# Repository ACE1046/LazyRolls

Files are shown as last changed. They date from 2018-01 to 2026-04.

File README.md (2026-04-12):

# LazyRolls

Automatic motorized roller blinds project.

Моторизированный привод для рулонных штор. Управление по Wi-Fi. Питание внешнее. Возможна интеграция в системы умного дома.




### Ссылки
Описание проекта: [https://mysku.club/blog/diy/62110.html](https://mysku.club/blog/diy/62110.html)\
Файлы для печати: [https://www.thingiverse.com/thing:2857899](https://www.thingiverse.com/thing:2857899)\
Видео работы: [https://www.youtube.com/watch?v=lvBh_m7pOAI](https://www.youtube.com/watch?v=lvBh_m7pOAI)

### Плагины для систем умного дома
[Domoticz](https://github.com/ACE1046/LazyRollsDomoticz)\
[Hubitat Elevation](https://github.com/yix/Hubitat/blob/master/drivers/LazyRolls.groovy) (Автор [yix](https://github.com/yix))\
Home Assistant (встроенная поддержка через MQTT Discovery с версии 0.09)\
[Homebridge](https://github.com/vitva/Lazyroll-settings-for-homebridge) (Автор Vitva)\
[Управление с пульта ИК / RF433](https://mysku.club/blog/diy/87912.html) (Автор SamoS)\
[Карточка управления шторами для HA](https://github.com/samoswall/pic-shutter-card) (Автор SamoS)\
[Android приложение для управления шторами](https://github.com/samoswall/LazyRoll-Android-App) (Автор SamoS)

### Структура директорий

Firmware - готовые прошивки\
Source - исходный код\
Source\data - файлы для SPIFFS. Иконка, css-стили, java scripts\
Board - файлы схемы и платы для DipTrace\
Board\Gerbers - gerber files для заказа плат на фабрике\
3D_parts - OpenSCAD и stl для печати

### Changelog

05.04.2018 v0.01 beta
* Более-менее рабочая версия с настройками. Не всё доделано, многого не хватает.

07.04.2018 v0.02 beta
* Автосоздание файлов CSS и favicon в SPIFFS при их отсутствии/обновлении.

28.04.2018 v0.03 beta
* Исправлен баг с закрытием шторы после перезагрузки.
* Добавлена работа по расписанию.

22.02.2019 v0.05 beta
* Управление двигателями идёт в прерывании, увеличилась плавность работы двигателя и отзывчивость интерфейса.
* Номера пинов 4 и 5 исправлены, теперь типичное подключение ABCD. Настройки менять не надо.
* Концевик можно инвертировать (нормальнозамкнутый - нормальноразомкнутый). Актуально для датчика Холла вместо концевика.
* Добавлен http-запрос /set?pos=X (X = 0 - 100, в процентах).
* Состояние можно получить в виде XML по адресу /xml.
* Прошивка откомпилирована с поддержкой модулей с флеш памятью PUYA.
* Отображается размер SPIFFS, ссылка на форматирование появляется при ошибке файловой системы.

16.03.2019 v0.06
* Добавлен протокол MQTT. Описание настроек http://imlazy.ru/rolls/mqtt.html

10.04.2019 v0.07
* Добавлена встроенная в esp8266 подтяжка пина концевика. На платах NodeMCU и тому подобных, отпадает необходимость во внешнем резисторе, R8 по схеме.
* Добавлена настройка безопасного порога, количество шагов, при которых штора игнорирует концевик, пока не выползет из зоны его действия. Для герконов и датчиков Холла можно установить значение больше стандартных 100.

02.06.2020 v0.08
* Сделан плавный пуск двигателя. Это чуть повысило мощность мотора и максимальную скорость, но незначительно. Пока в черновой реализации и без какой-либо настройки.
* Прошивка проверена и скомпилирована с Arduino core for ESP8266 v2.7.1. Исправило отваливание wi-fi сети в некоторых случаях.
* Исправлен баг в JavaScript, из-за которого иногда лагал веб интерфейс, при загрузке страниц и сразу после.
* Во время движения по MQTT в формате JSON сообщается не только текущее положение, но и точка назначения (destination, в процентах).
* Синий светодиод теперь используется. Он кратко моргает при подаче питания. После каждой неудачной попытки подключиться к основной
сети зажигается на 1 секунду. Если к сети подключиться с трёх попыток не вышло, светодиод горит непрерывно, значит создана собственная WiFi сеть.
(Оранжевый светодиод программно не управляется, подключен напрямую к питанию. Его можно только отпаять/откусить/заклеить.)
В нормальной работе функцию диода можно указать в настройках, а также менять по http/mqtt. Более подробно [imlazy.ru/rolls/led.html](http://imlazy.ru/rolls/led.html).
* Отображается напряжение питания для новых плат. На старых, при желании, можно допаять два резистора. Цепочка Vin - 150K - esp_adc - 10K - GND.
* Исправлен баг с максимальным количеством шагов игнорирования концевика при опускании шторы. Теперь работают значения более 255. До 65000. Актуально для герконов и датчиков Холла. Спасибо acu73.
* Исправлен баг с невозможностью указать порт MQTT сервера более 9999. Спасибо George Tkachenko.

29.01.2021 v0.09
* Исправлен баг со сбивающимся временем.
* Пресеты для точного позиционирования шторы. Актуально для штор день/ночь. Положения задаются в настройках. Могут использоваться в расписании.
* Добавлены команды для MQTT. "=NNNNN" (без кавычек) - позиционирование шторы в шагах. "@N" - переход к пресету N.
* Добавлен http-запрос /set?steps=NNNNN (NNNNN = 0 - 65000, в шагах мотора).
* Добавлен http-запрос /set?preset=N (N = 1 - 5). Переход в заданное положение.
* Добавлено автоматическое перенаправление на страницу настроек при подключении к шторе в режиме точки доступа (первоначальная настройка).
* Добавлены MQTT-комманды open и close. Равнозначны on и off. Для удобства интеграции с HA.
* Добавлен MQTT Discovery для Home Assistant. Включается в настройках, автоматически добавляет штору в HA.
* Библиотека для работы с MQTT изменена с AdaFruit на PubSubClient (by Nicholas O'Leary).
* Концевик может быть установлен на полностью закрытое положение, вместо открытого. Например, для жалюзи.
* Проценты в MQTT командах и статусах можно поменять на обратные, т.е. 0% значит закрыто, 100% - открыто. Так по умолчанию считает Cover в Home Assistant.

30.03.2021 v0.10
* Исправлен баг с количеством шагов игнорирования концевика. Фактическое было в 8 раз меньше указанного в настройках.
* Повышена точность измерения напряжения, на платах с резисторами на ADC.
* Добавлена поддержка драйверов Step/Dir моторов (например, NEMA17). Можно подключать двигатели и драйвера от 3D принтеров. Распиновка пока фиксированная, En 4, Step 13, Dir 12.
* Минимальное время шага уменьшено до 50 мкс (было 100). Этого должно хватить, чтобы крутить обычный NEMA17 на практически максимальной скорости при 1/16 шага.
* В MQTT добавлен топик присутствия (alive/живой). В него отправляется "online" при подключении к MQTT и "offline" при отключении, в т.ч. аварийном, по "завещанию" (LWT). В Home Assistant используется как availability topic, для определения состояния привода.
* В настройках можно изменить количество шагов, которое привод прокручивает вверх в поисках концевика после предполагаемого нуля. Если поставить 0, запаса не будет. Если поставить большое число, будет дольше крутить вверх, пока не сработает концевик. Но в случае проблем с концевиком, может привести к перегреву мотора или поломке шторы. Менять не рекомендуется.
* Добавлена возможность подключения кнопки для управления. Подключается на Gnd и один из пинов GPIO 0(DTR)/2/3(RX), который выбирается в настройках. При движении нажатие кнопки останавливает штору, двойное нажатие - останавливает и перезапускает в противоположном направлении. Долгое нажатие (1 секунда) - отправляет в первый пресет или во второй, если штора уже в первом.
* Синий диод можно настроить на мигание при нажатии на кнопку.
* Легкий редизайн внешнего вида, в первую очередь мобильной версии. JS-код вынесен в отдельный файл в spiffs.
* Статичные файлы сжаты gzip'ом.
* Обновлена страница /update, добавлены подсказки по перепрошивке.

05.08.2021 v0.11
* Экспериментальная фича: режим мастер/ведомый по проводу. Подробнее [imlazy.ru/rolls/master.html](http://imlazy.ru/rolls/master.html).
* Помимо кнопки, можно задействовать ещё один дополнительный вход. Например, для геркона, определяющего открытие окна. Статус передаётся по MQTT в выбранный топик.
* Новый топик MQTT, сообщает в формате JSON состояние (ip, rssi, uptime, voltage, aux_input). При включенном HA MQTT Discovery, автоматически добавляет эти сенсоры в Home Assistant.
* (v0.11.2) Исправлен баг с получением времени по NTP при старте.

09.11.2021 v0.11.3
* Исправлен баг с отображением hostname в сети. В XML статус добавлен hostname. Разрешена отдача XML сторонним страницам (CORS). Спасибо Samos.

27.01.2022 v0.12
* В MQTT Discovery добавлены фичи Home Assistant 2021.11: ссылка на страницу конфигурации (visit device), доп. статусы попадают в раздел "Diagnostic".
* Добавлены команды click, longclick для MQTT и /set?click, /set?longclick для HTTP. Делают то же самое, что и кнопка управления (открыть/закрыть/стоп; пресет1/2). Для работы этих команд, включать аппаратную кнопку не требуется.
* Можно изменить название шторы в настройках, для удобства. Отображается в заголовке окна и в поле name в XML.
* Настройка статического IP.
* При прошивке на чистый модуль поле SSID остаётся пустым и привод сразу стартует в режиме точки доступа, а не пытается приконнектиться к несуществующей сети lazyrolls.
* Исправлена (надеюсь) верстка страницы расписания.
* Проект модифицирован для компиляции в PlatformIO, но можно откомпилировать и в ArduinoIDE. Часть кода переписана для экономии памяти. Arduino core for ESP8266 обновлено до v3.0.2.
* Добавлен лог событий. Открывается в веб-интерфейсе по ссылке из блока информации. Лог на английском, но думаю там и так понятно. Отображаются основные события, причина перезагрузки, отвалы от сети и mqtt-сервера, срабатывание концевика в движении, синхронизация времени. Для отладки возможных проблем.

10.12.2022 v0.13
* Поддержка приемника 433МГц.
* Восход и закат в расписании.
* Поддержка двух физических кнопок с возможностью выбирать действие по нажатию и, в режиме мастера, кем управлять. Можно сделать раздельные кнопки Открыть и Закрыть, а можно разделить кнопки для управления только этой шторой и всей группой.
* На главную страницу добавлены кнопки пресетов. В режиме мастера добавлен выбор, кем управлять, всеми, этой шторой или ведомыми.
* В режиме мастера можно в расписании раздельно управлять ведущим и ведомыми.
* Можно задать пароль для режима точки доступа, создаваемой после включения привода при отсутствии Wi-Fi.

26.01.2023 v0.13.1
* Добавлена единица измерения для напряжения в Home Assistant.

20.04.2023 v0.14
* Добавлена поддержка моторов постоянного тока, в том числе с энкодером. Подробнее [imlazy.ru/rolls/motor.html](http://imlazy.ru/rolls/motor.html).
* Добавлен второй концевик, на противоположной стороне.
* Добавлены команды MQTT. По команде "report" сообщает по MQTT свой статус. Командой "endstop" можно эмулировать нажатие концевика, например, zigbee датчиком открытия двери.
* По MQTT отправляются статусы open / opening / close / closing / stopped для Home Assistant.
* Добавлен gratuitous ARP. Привод постоянно сообщает свой IP в сети. Включается автоматически, если не используется MQTT. Может предотвратить некоторые случаи недоступности привода в сети.
* Сенсор Uptime в Home Assistant заменен на сенсор Last Restart Time. В mqtt топик info отправляются и аптайм, как раньше, и время рестарта.

16.01.2024 v0.15
* Плавный старт шагового мотора стал более плавным.
* Arduino core for ESP8266 обновлено до v3.1.2.
* Откомпилированные прошивки теперь универсальны, подходят для любого размера флэш-памяти.
* Изменения в MQTT: Обновлена интеграция с Home Assistant для совместимости с последней версией. Для наименования устройства используется не сетевое имя (hostname), а название (name), если оно заполнено в настройках. Недопустимые символы заменяются на подчеркивание, hostname теперь может содержать точку, без ошибки в логах HA.
* Retained команды удаляются и игнорируются при подключении к MQTT.
* В xml статус добавлены вход aux (если настроен), поле 'master' (значение 'yes' для мастера, 'no' - все остальные) и список пресетов и их значений.
* В настройках можно выбрать две скорости мотора. Их можно использовать, к примеру, для ручного (быстро) и автоматического (тихо) управления или для разных скоростей вверх и вниз. Вторую скорость можно использовать при управлении по расписанию, http, mqtt, rf и кнопками.
* Все настройки можно скачать/загрузить в виде файла на странице обновления прошивки.
* Команды для сброса положения и поиска нуля заново: 'zero' по mqtt, /set?zero по http. Команда 'reboot' по mqtt для перезагрузки.
* Сторожевой пингер. Включается в настройках. Раз в минуту пингует заданный IP (например, wifi-роутер). После неудачи, пинги повторяются каждые 10 секунд. 4 пропущенных подряд пинга записываются в Log. После 7 пропущенных пингов выполняется указанное в настройках действие (логирование / переподключение / перезагрузка). Интервал пинга и количество пропущенных пингов можно изменить константами PINGER_INTERVAL_S / PINGER_REPEAT_INTERVAL_S / PINGER_WARN / PINGER_ACTION в прошивке, при необходимости.
* Режим мастер/ведомый по WiFi. Теперь в дополнение к ведомым по проводу можно добавить ведомых по IP. На них распространяются все возможности управления, как и у проводных. Поддерживается до 10 ведомых в 5 группах (те же, что у проводных. В одной группе могут быть как проводные, так и беспроводные ведомые). Подробнее [imlazy.ru/rolls/master.html](http://imlazy.ru/rolls/master.html).
* В настройках добавлены кнопки включения WiFi у проводных ведомых, с отображением их IP после подключения к сети, для удобства настройки ведомых.
* В расписании можно установить самое раннее время срабатывания по солнцу, например "на рассвете, но не ранее 07:00".
* Положение шторы можно сохранять во flash-памяти, оно не теряется при перезагрузке. Включается в настройках. Не рекомендуется использовать без необходимости, ресурс памяти на запись ограничен, это может сократить срок службы. Если перезагрузка произойдет во время движения, положение не восстановится и потребуется поиск нуля.

17.01.2024 v0.15.2
* Исправлен баг, не появлялись кнопка Scan и пункт добавления IP в настройках wifi ведомых.
* Исправлен баг в wifi мастер/слейв режиме.

18.01.2024 v0.15.3
* Исправлен баг работы wifi мастер/слейв от аппаратных кнопок.
* При смене направления движения штора останавливает и плавно начинает двигаться в обратную сторону.
* Включена поддержка mDNS.

06.03.2025 v0.15.4
* Поддержка ESP32. Пока что тестовый вариант для ESP32-C3. Должно работать с ABCD мотором (другие пока не проверялись). Компиляция в Platformio IDE (в Arduino IDE не проверялось).

10.04.2026 v0.15.6
* Для шаговых двигателей добавлена плавная остановка при движении вниз. В настройках можно включить удержание мотора в течение ~5 сек после остановки, для предотвращения разматывания шторы по инерции.
* Для DC моторов можно регулировать скорость через PWM не только на драйверах с отдельным входом PWM, но и через пины управления вращением, если драйвер поддерживает.
* На esp32c3 отображается температура чипа.
* Добавлена поддержка выбора часового пояса в формате POSIX с учётом перевода на летнее время. Добавлен справочник часовых поясов по городам.
* Диапазон уровней солнца над горизонтом в расписании увеличен до [-10, 10] градусов.
* Добавлена функция принудительного поиска нуля для кнопок и RF пульта. К командам для сброса нуля ('zero' по mqtt, /set?zero по http) добавлены 'gotozero' и /set?gotozero для поиска нуля прямо сейчас.

### Authors

* **ACE** - [e-mail](mailto:ace@imlazy.ru)

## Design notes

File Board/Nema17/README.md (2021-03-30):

# LazyRolls with NEMA17

Поддержка Step/Dir драйверов шаговых двигателей добавлена с версии v0.10 прошивки.\
Step/Dir drivers support added to v0.10 firmware.

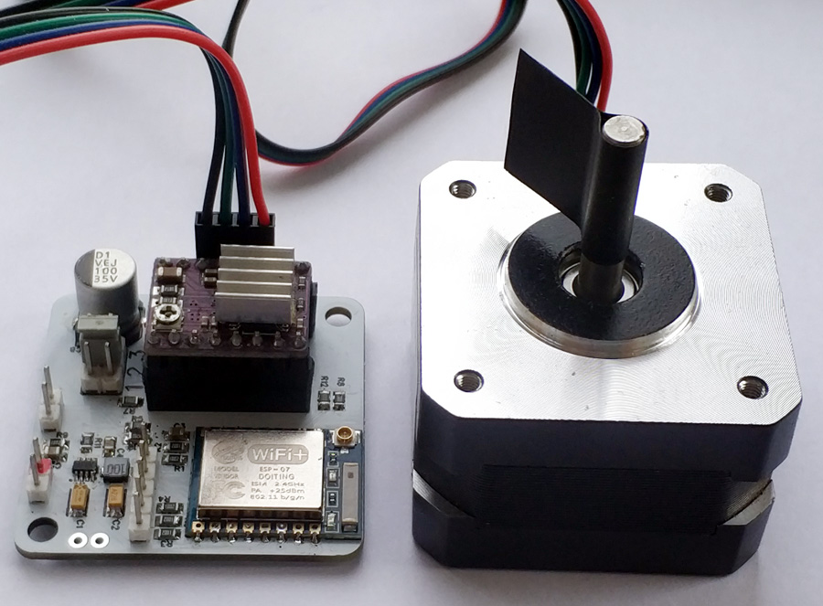
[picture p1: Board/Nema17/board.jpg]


### Подключение / Wiring

Enable - GPIO4\
Step - GPIO13\
Dir - GPIO12

### Плата / Board

Размер платы равен размеру мотора NEMA17, 42х42мм\
Board size equal to NEMA17 motor size, 42x42mm

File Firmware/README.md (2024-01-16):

### Прошивки для привода LazyRolls

Начиная с версии 0.15 прошивка стала универсальной (_auto), на любой размер памяти. И переименована по имени проекта, LazyRoll.\
Обновлять прошивку по воздуху, через интерфейс штор, можно (и нужно) прямо архивом .gz, не распаковывая.\
Файлы *.1MByte.bin для плат с модулем ESP07.\
Файлы *.4MByte.bin для собранных на основе Wemos, NodeMCU и т.д.\
Размер памяти можно уточнить в веб-интерфейсе привода.

Обновление прошивки на ту же версию или более новую сохраняет все настройки. Обновление на предыдущую - стирает настройки, включая WiFi.

### LazyRolls firmware

Starting from version 0.15, the firmware became universal (_auto), for any memory size. And renamed after the project name, LazyRoll.\
When updating the firmware over the air, through web interface, upload .gz archive, without unpacking it.\
Choose *.1MByte.bin for boards with ESP07 module\
Choose *.4MByte.bin for devices based on Wemos, NodeMCU, etc\
Memory size can be seen in web-interface.

Updating to newer version will preserve settings, but downgrading to previous will erase all settings, including WiFi.

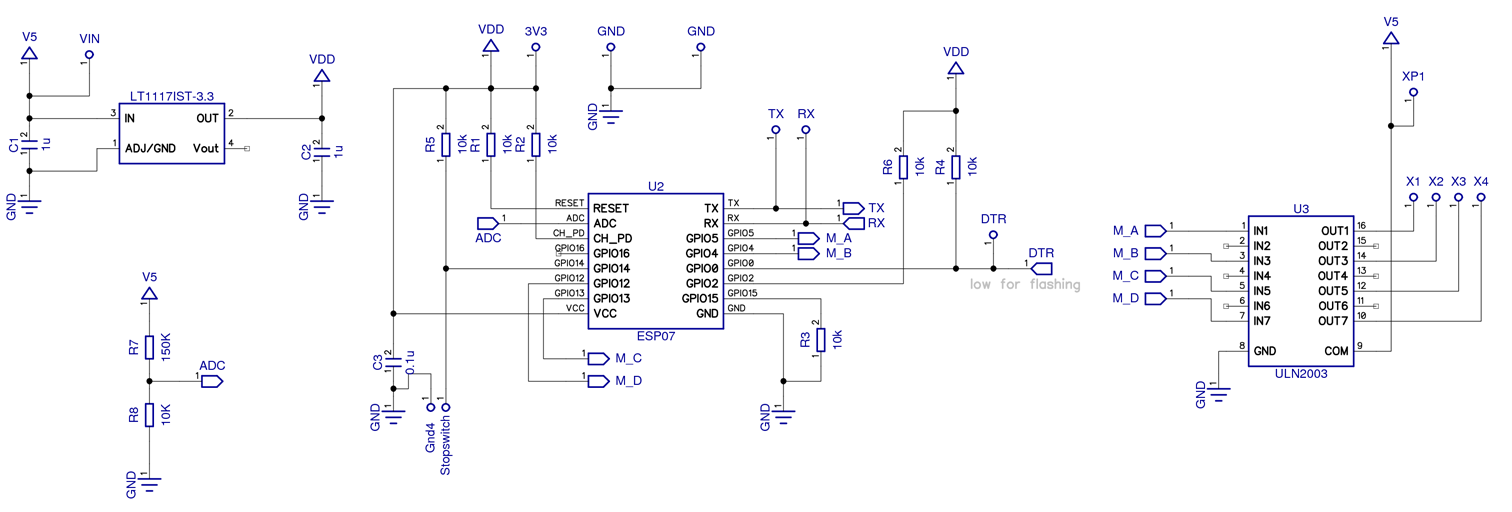
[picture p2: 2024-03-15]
Board/scheme.png

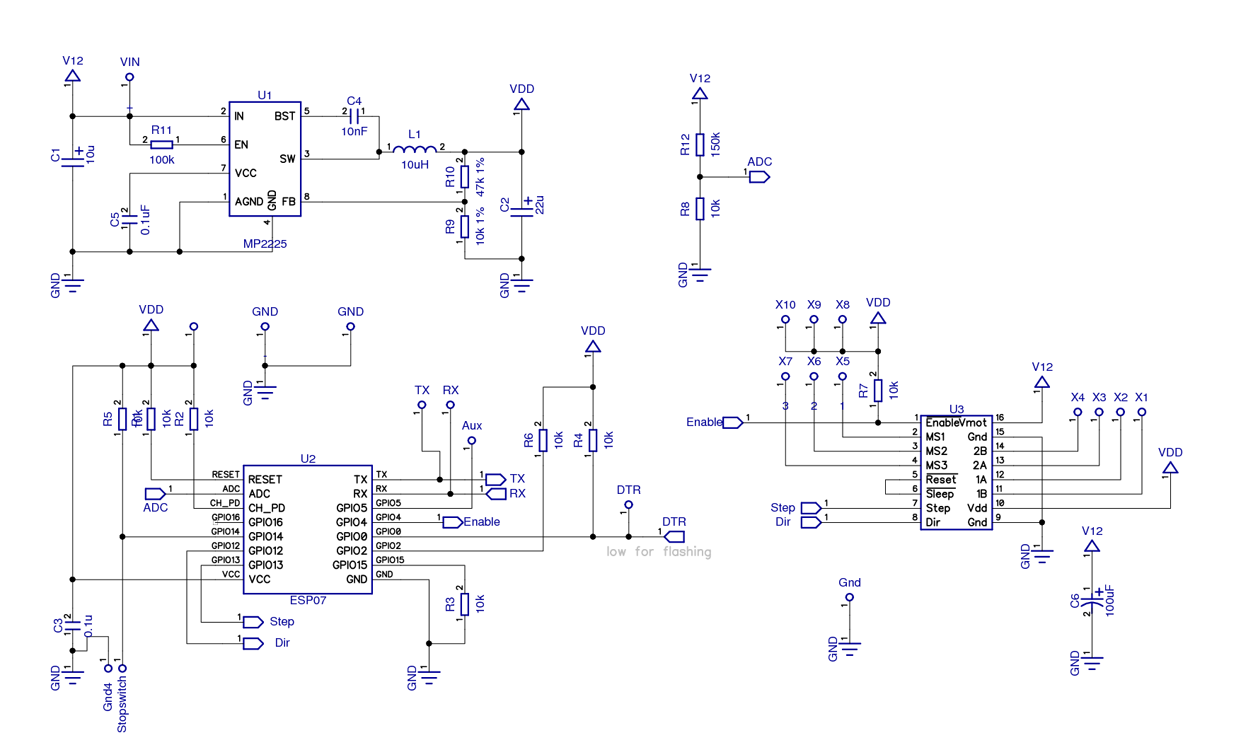
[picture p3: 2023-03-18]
Board/Nema17/LazyRolls_v1.2_nema17.png

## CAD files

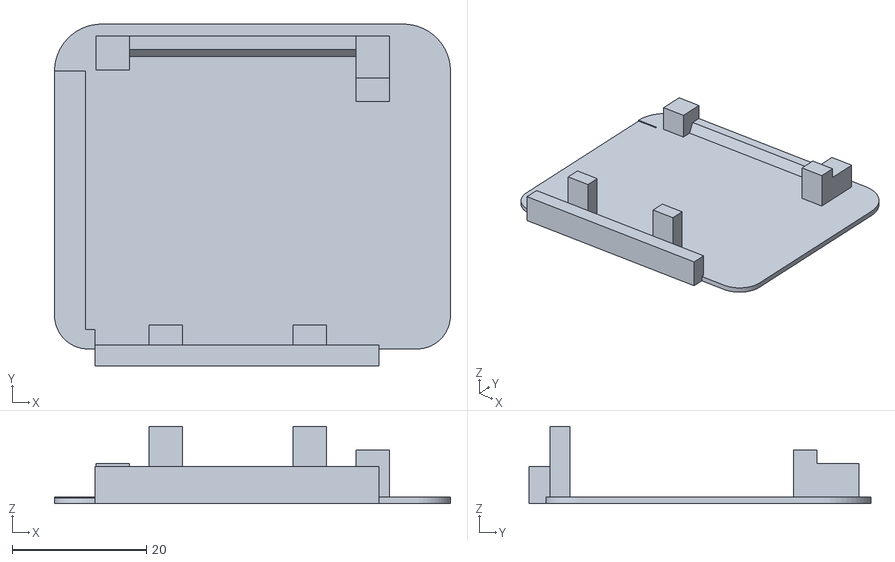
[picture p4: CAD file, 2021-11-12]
3D_parts/cap.stl
59.0 x 50.9 x 11.5

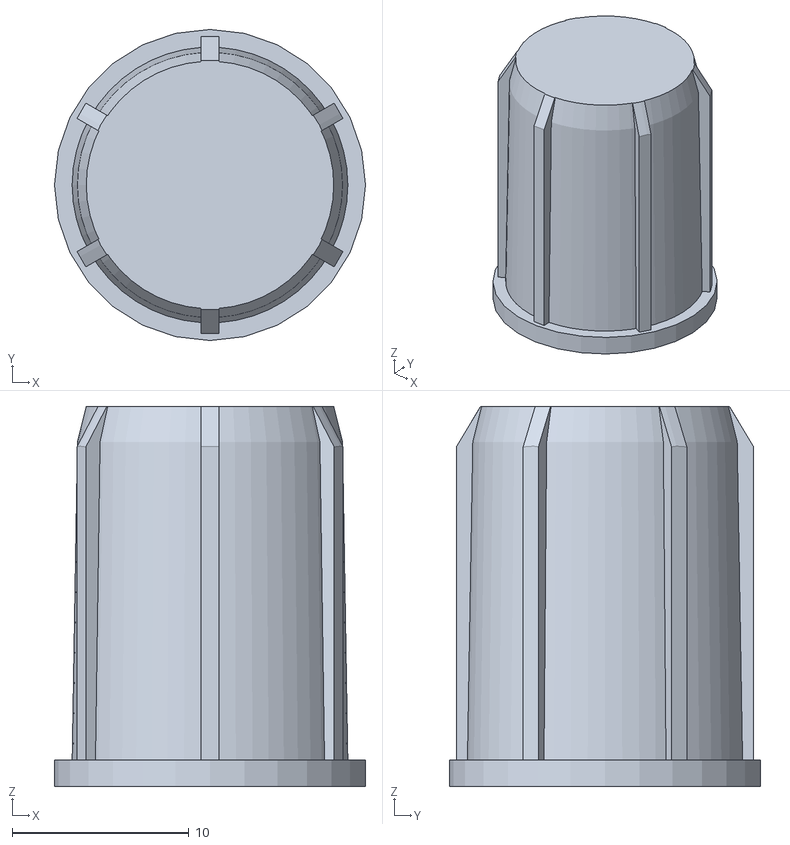
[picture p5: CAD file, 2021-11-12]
3D_parts/Shaft.stl
17.6 x 17.6 x 21.5

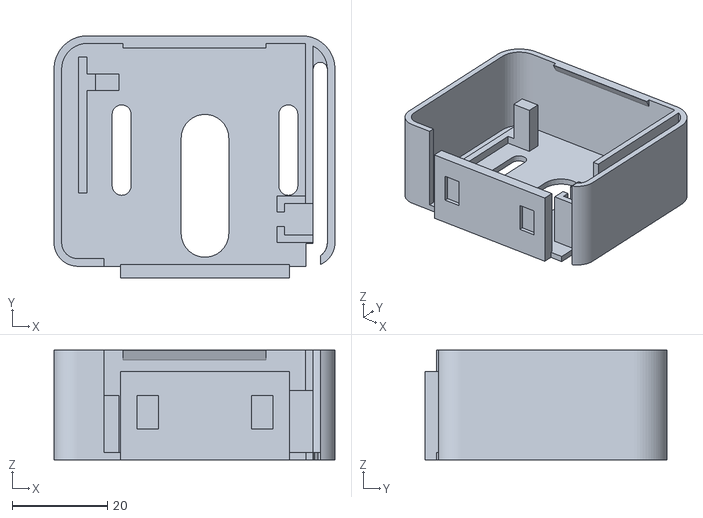
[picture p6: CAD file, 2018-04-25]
3D_parts/Motor_bracket.stl
59.0 x 50.9 x 23.0

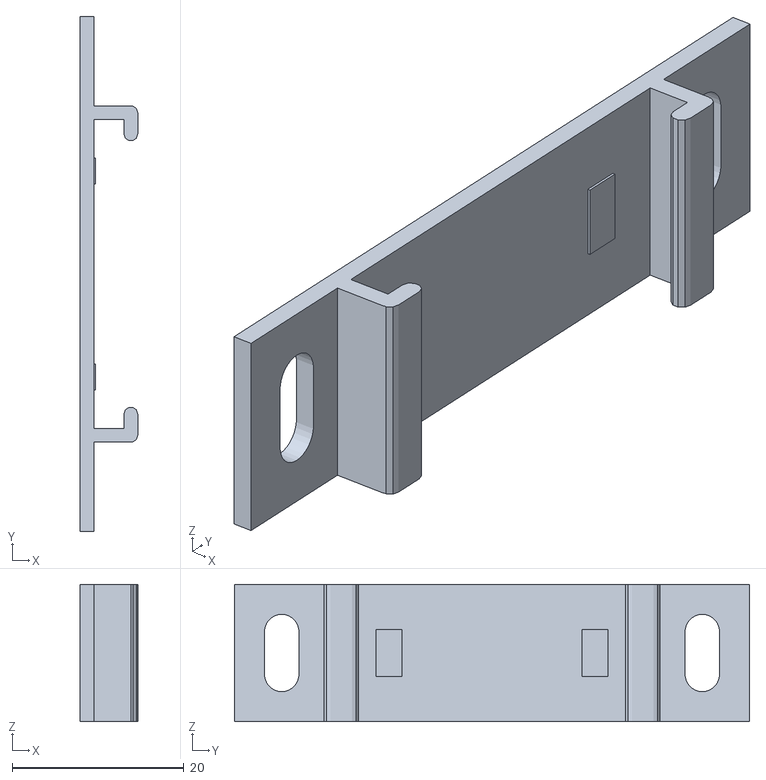
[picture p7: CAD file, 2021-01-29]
3D_parts/mount_screw.stl
6.70 x 60.0 x 16.0

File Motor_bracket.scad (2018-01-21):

base_h=35.5;
base_w=17;
base_t=3.0;
base_space=base_h+7; //42;

fix_h=4.5;
fix_w=7;
fix_d=24/2;

arm_t=1.5;
arm_l=46.5;
arm_w=10;
arm_dist=35/2;
arm_hole=4;
arm_hole_l1=15;
arm_hole_l2=30;

side_t=1.6;
full_h=59;
full_w=21.5;
back_r=5;
front_r=7;
sw_hole=3;
sw_t=1.6;
b_o=1;

motor_hole_w=10;
motor_hole_l=30;
motor_shift=2.2;

//micro switch
msw_w=6+0.6;
msw_h=7;
msw_l=13;
msw_t=1.6;
msw_conn=3;

// cap
cap_t=1.0;
cap_sp=0.4; // space
cap_fix_h=5;
cap_fix_t=2;
cap_fix_w=5;
cap_fix_ofs=4.5;
lock_h=2;
lock_w=30;

module arm()
{
	hull()
	{
		translate([0, arm_hole_l1, -arm_t-1]) cylinder(h=arm_t+2, d=arm_hole, $fn=20);
		translate([0, arm_hole_l2, -arm_t-1]) cylinder(h=arm_t+2, d=arm_hole, $fn=20);
	}
}

module sides(hh, r_b, r_f, b, shrink)
{
	hull()
	{
	translate([ full_h/2-r_b, r_b-side_ofs, -b]) cylinder(h=hh+arm_t, r=r_b-shrink);
	translate([-full_h/2+r_b, r_b-side_ofs, -b]) cylinder(h=hh+arm_t, r=r_b-shrink);
	translate([ full_h/2-r_f, arm_l-r_f, -b]) cylinder(h=hh+arm_t, r=r_f-shrink);
	translate([-full_h/2+r_f, arm_l-r_f, -b]) cylinder(h=hh+arm_t, r=r_f-shrink);
	}
}

side_ofs=base_t-b_o;

module base()
{
	translate([motor_shift,0,0]) difference()
	{
		translate([-base_h/2, -base_t, -arm_t]) cube([base_h, base_t, base_w+arm_t]);
		translate([-fix_d-fix_h/2, -base_t-1, arm_w/2]) cube([fix_h, 2, fix_w]);
		translate([ fix_d-fix_h/2, -base_t-1, arm_w/2]) cube([fix_h, 2, fix_w]);
	}

	difference()
	{
		sides(full_w, back_r, front_r, arm_t, 0, $fn=70);
		sides(full_w+2, back_r, front_r, 0, side_t, $fn=40);
		translate([-base_space/2+motor_shift, -side_t-1, 0]) cube([base_space+sw_hole, side_t+2, full_w+1]);
		mirror([1,0,0])
		translate([-arm_dist-motor_shift, 0, 0]) arm();
		translate([-arm_dist+motor_shift, 0, 0]) arm();
		//translate([-motor_hole_w/2+motor_shift, 0, -base_t-1]) cube([motor_hole_w, arm_l-side_t, base_t+2]);
		hull()
		{
			translate([motor_shift, motor_hole_w/2, -base_t-1]) cylinder(d=motor_hole_w, h=base_t+2, $fn=30);
			translate([motor_shift, -motor_hole_w/2+motor_hole_l, -base_t-1]) cylinder(d=motor_hole_w, h=base_t+2, $fn=30);
		}
		
		
		translate([full_h/2-sw_t-sw_hole, back_r-side_ofs, -arm_t-1]) cube([sw_hole, arm_l+side_ofs-back_r-front_r, arm_t+full_w+2]);
		translate([full_h/2-sw_t-sw_hole/2, arm_l-front_r, -arm_t-1]) cylinder(h=arm_t+full_w+2, r=sw_hole/2, $fn=10);
		intersection()
		{
			translate([ full_h/2-back_r, back_r-side_ofs, -arm_t-1]) cylinder(h=full_w+arm_t+2, r=back_r-sw_t, $fn=30);
			translate([ full_h/2-sw_t-sw_hole, back_r-side_ofs-10+0.01, -arm_t-1]) cube([10,10,full_w+arm_t+2]);
		}
		translate([+base_space/2+motor_shift, -side_t-1, -arm_t-1]) cube([sw_hole, side_t+2, full_w+1]);

	}

	translate([full_h/2-sw_t-sw_hole-msw_h-msw_t+msw_h+msw_t-side_t, back_r-side_ofs+msw_w+msw_t*2-side_t, 0]) 
	cube([side_t, arm_l-(back_r-side_ofs)-(msw_w+msw_t*2), full_w]);
	// microswitch
	translate([full_h/2-sw_t-sw_hole-msw_h-msw_t, back_r-side_ofs, 0]) 
	difference()
	{
		cube([msw_h+msw_t, msw_w+msw_t*2, msw_l]);
		translate([msw_t, msw_t, 0]) cube([msw_h+1, msw_w, msw_l+1]);
		translate([-1, msw_t+msw_w/2-msw_conn/2, 0]) cube([msw_t+2, msw_conn, msw_l+1]);
	}

	// PCB holder
	translate([-full_h/2+side_t+2+1.5+1.5+2.5, 35, 0]) cube([5, 3.5, 12]);
	translate([-full_h/2+side_t+2+1.5, 35, 0]) cube([5+1.5+2.5, 3.5, 2]);
	translate([-full_h/2+side_t+2+1.5, 12, 0]) cube([1.8, 30, 2]);

	%translate([-full_h/2+side_t+2, 0, 0])
	{
		color("green") cube([1.5, 43.2, 21]);
		color("blue") translate([1.5,21.9,3])cube([1.5, 21, 16]);
		color("grey") translate([3,23.5,5])cube([2.5, 15, 12]);
	}

	// lock
	hull()
	{
		translate([-lock_w/2, arm_l-side_t-lock_h/2, full_w-0.1]) cube([lock_w, side_t, 0.1]);
		translate([-lock_w/2, arm_l-side_t, full_w-lock_h]) cube([lock_w, side_t, 0.1]);
	}
}

module cap()
{
  difference()
	{
		hull()
		{
			$fn=50;
			translate([ full_h/2-back_r, back_r-side_ofs, 0]) cylinder(h=cap_t, r=back_r);
			translate([-full_h/2+back_r, back_r-side_ofs, 0]) cylinder(h=cap_t, r=back_r);
			translate([ full_h/2-front_r, arm_l-front_r, 0]) cylinder(h=cap_t, r=front_r);
			translate([-full_h/2+front_r, arm_l-front_r, 0]) cylinder(h=cap_t, r=front_r);
		}
		translate([full_h/2-sw_t-sw_hole, back_r-side_ofs-100, -cap_t+cap_sp]) cube([sw_hole+100, arm_l+side_ofs-back_r-front_r+100, cap_t]);
		translate([+base_space/2+motor_shift, -side_t-1, -cap_t+cap_sp]) cube([sw_hole, side_t+2, cap_t]);
	}
	translate([motor_shift-base_space/2+cap_sp, -base_t, -full_w+base_w]) cube([base_space-cap_sp, base_t+cap_sp, full_w-base_w+cap_t]);
	translate([motor_shift-base_h/2+cap_fix_ofs, cap_sp, -(full_w-base_w+cap_t+cap_fix_h)]) cube([cap_fix_w, 3, full_w-base_w+cap_t+cap_fix_h]);
	translate([motor_shift+base_h/2-cap_fix_ofs-cap_fix_w, cap_sp, -(full_w-base_w+cap_t+cap_fix_h)]) cube([cap_fix_w, 3, full_w-base_w+cap_t+cap_fix_h]);
	translate([-full_h/2+side_t+2+1.5+1.5+2.5, 35, -cap_fix_h-2]) cube([5, 3.5, cap_fix_h+2]);
	translate([-full_h/2+side_t+2+1.5+1.5+2.5, 35, -cap_fix_h]) cube([5, arm_l-35-side_t-cap_sp, cap_fix_h]);

	// front lock
	hull()
	{
		translate([-full_h/2+side_t+2+1.5+1.5+2.5, arm_l-side_t-2-cap_sp-lock_h/2,  0]) cube([full_h-front_r-side_t-(2+1.5+1.5+2.5), 2, 0.1]);
		translate([-full_h/2+side_t+2+1.5+1.5+2.5, arm_l-side_t-2-cap_sp, -lock_h]) cube([full_h-front_r-side_t-(2+1.5+1.5+2.5), 2, 0.1]);
	}

	translate([full_h/2-sw_t-sw_hole-side_t-5, 35-5+arm_l-35-side_t-cap_sp, -cap_fix_h]) cube([5, 5, cap_fix_h]);
	// mswitch
//	translate([full_h/2-sw_t-sw_hole-msw_h-msw_t, back_r-side_ofs, -(full_w-msw_l)]) 
//		cube([msw_h+msw_t, msw_w+msw_t*2, full_w-msw_l]);
}

//base(); //translate([0, 0, full_w+0.2]) cap();
rotate([0,180,0]) cap();

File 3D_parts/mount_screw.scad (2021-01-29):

// base plate
bw=16;
bl=60;
bt=1.6;

// mount
mw=16;
ml=36;
mh=3.5;
mt=1.6;
ma=2.5; // arms

//pads
pw=5.5;
pl=3;
ph=0.2;
po=12;

// holes
hd=4;
hl=5;
ho=24.5;

module hole(offset, diam)
{
  hull()
  {
    translate([-hl/2, offset, -1]) cylinder(h=bt*2+2, d=diam, center=true, $fn=30);
    translate([ hl/2, offset, -1]) cylinder(h=bt*2+2, d=diam, center=true, $fn=30);
  }
}

//rotate([0,90,0])
{
    difference()
    {
      union()
      {
        translate([-bw/2, -bl/2, -bt]) cube([bw, bl, bt]);

        translate([0, po,0]) cube([pw, pl, ph*2], center=true);
        translate([0,-po,0]) cube([pw, pl, ph*2], center=true);
      }
      hole(-ho, hd);
      hole(ho, hd);
    }

    translate([-bw/2, -ml/2-mt, -bt]) cube([mw, mt, bt+mh+mt/2]);
    translate([-bw/2,  ml/2, -bt]) cube([mw, mt, bt+mh+mt/2]);

    hull()
    {
        translate([0, -ml/2+ma-mt/2, mh+mt/2]) rotate([0, 90, 0]) cylinder(h=mw, d=mt, center=true, $fn=10);
        translate([0, -ml/2-mt/2, mh+mt/2]) rotate([0, 90, 0]) cylinder(h=mw, d=mt, center=true, $fn=10);
    }

    hull()
    {
        translate([0, ml/2-ma+mt/2, mh+mt/2]) rotate([0, 90, 0]) cylinder(h=mw, d=mt, center=true, $fn=10);
        translate([0, ml/2+mt/2, mh+mt/2]) rotate([0, 90, 0]) cylinder(h=mw, d=mt, center=true, $fn=10);
    }
}

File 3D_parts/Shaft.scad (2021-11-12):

d=15.6;
l=20;
cone=2;

// base
bd=d+2;
bl=1.5;

// shaft
sd=5.3;
sw=3.2;
sl=7;

difference()
{
	intersection()
	{
		union()
		{
			translate([0, 0, -bl]) cylinder(h=bl, d=bd);
			translate([0, 0, 0]) cylinder(h=l-cone, d1=d, d2=d-0.6, $fn=50);
			translate([0, 0, l-cone]) cylinder(h=cone, d1=d-0.6, d2=d-0.6-cone/2, $fn=50);

			
			rotate([0, 0,  0]) translate([0, 0, l/2]) cube([1, d+1.2, l], center=true);
			rotate([0, 0, 60]) translate([0, 0, l/2]) cube([1, d+1.2, l], center=true);
			rotate([0, 0,-60]) translate([0, 0, l/2]) cube([1, d+1.2, l], center=true);
		}
		translate([0, 0, -bl-0.1]) cylinder(h=l+bl+0.2, d1=l*2, d2=d-0.6-cone/2, $fn=50);
	}
	intersection()
	{
		translate([0, 0, -bl-0.1]) cylinder(h=sl, d=sd, $fn=40);
		translate([0, 0, sl/2-bl-0.1]) cube([sw, sd, sl], center=true);
	}
}

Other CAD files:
3D_parts/Motor_bracket.scad

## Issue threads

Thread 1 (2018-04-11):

Ссылка на муську в README

Bougakov, 2018-04-11:
Пожалуйста, поставьте ссылку на свою статью https://mysku.ru/blog/diy/62110.html в README.md, а то ж не найти потом... Спасибо!

ACE1046, 2018-04-11:
Благодарю! Совсем забыл про это.
Сделано.

T-REX-XP, 2019-08-19:
Во время тестирования, замечаю странное поведение. Шторы не работатю вместе на одном окне. То ли теряют подключение к wifi, толи в сон входят. Пробовал разносить по разным блоками питания и по разным сетям wifi. Первое время после старта вроде доступны обе админки и можно управлять, но когда на ночь оставляешь что утром только одна открывается.

Closed 2018-04-11.

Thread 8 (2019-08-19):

Шторы не работают одновременно

T-REX-XP, 2019-08-19:
Во время тестирования, замечаю странное поведение. Шторы не работатю вместе на одном окне. То ли теряют подключение к wifi, толи в сон входят. Пробовал разносить по разным блоками питания и по разным сетям wifi. Первое время после старта вроде доступны обе админки и можно управлять, но когда на ночь оставляешь что утром только одна открывается.

Closed 2019-09-24.

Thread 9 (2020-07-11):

Добавить ссылку на Hubitat driver

yix, 2020-07-11:
Я запили LazyRolls драйвер для IoT хаба Hubitat Elevation. Хочу поделиться его кодом, возмоно кому-то окажется полезным.

https://github.com/yix/Hubitat/blob/master/drivers/LazyRolls.groovy

Closed 2020-07-13.

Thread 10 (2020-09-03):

Кнопки для управления.

VadimSVI, 2020-09-03:
Отличная работ! Считаю, что кроме удаленного управления, не хватает физических кнопок для управления шторами. Не всегда удобно заходить на веб интерфейс, а наличие отдельных кнопок позволит при необходимости быстро управлять ими.

ACE1046, 2021-03-30:
Возможность подключить физическую кнопку добавлена в версии v0.10

Closed 2021-03-30.

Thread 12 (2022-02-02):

Неявная работа после сброса питания (save/restore position in eeprom?)

andrew-moiseyev, 2022-02-02:
Антон, спасибо за проект!

Есть один неочевидный и нигде не отражённый момент - после подачи питания кнопки теста работают корректно, нажатие "вниз" делает "вверх". Если кому-то тоже будет непонятно - в setup:
```
// start position is twice as fully open. So on first close we will go up till home position
position=ini.full_length*2+ini.up_safe_limit;
```

Предложения:
1. Сделать это очевидным - отразить в документации, выдавать предупреждение в web-части, отдавать в mqtt.
2. Всё же сохранять в eeprom - говорят про 100.000 записей и неограниченное чтение. Если писать 10 раз в день - это 27 лет. Делаем метод SetPosition, в нём присваивание position и запись в eeprom. В сетапе, соответственно, считывание и присваивание напрямую. Для подстраховки от отключения питания во время работы мотора - сохранять признак isRolling, если после возобновления питания он true - работать по Вашему алгоритму.

ACE1046, 2022-02-02:
Спасибо за фидбек!

Да, этот момент у многих пользователей вызывает вопросы при первоначальной настройке. Где-то с 0.10й версии прошивки я добавил на главном экране, с большими кнопками, комментарий внизу:
> Напоминание. После перезагрузки, по любой команде (открыть или закрыть) штора вначале едет вверх, до концевика, чтобы найти нулевую точку. Это нормально.

Вопросов стало меньше (в почте, личке, тг-канале). Над документацией, конечно, ещё работать и работать. При первом старте, пожалуй, больше ничего не сделать.

При обычной работе это не должно быть заметно вообще, если шторы используются в режиме полного открывания/закрывания. И если питание не отключалось настолько, что был пропущен очередной момент переключения. Открытая штора (у концевика) закрывается сразу, закрытая - так и так едет в сторону концевика. Проблема только если из [полу]закрытого состояния получаем команду на закрытие или определенный процент. Имхо, не такой уж частый сценарий.

Сохранять положение я уже думал. Наверное, сделаю, хотя бы для пробы. Вообще, у esp8266 нет eeprom. Можно использовать часть внешней флеш-памяти программ. Китайцы в модули паяют разные чипы, разных производителей, разного качества. Сколько там циклов, я не знаю. Хорошо, если стандартные для микроконтроллеров 10000. При минимуме 4 записи в сутки (два цикла, запись перед и после) - 7 лет. Терпимо, если так. Конечно, можно будет провести ускоренное испытание, для гарантии. И использовать распределение записи на несколько ячеек.

Ещё момент, почему я изначально не хотел так делать, неизвестно, что вообще происходило в то время, что не было питания. Может штору механически закрыли. А привод помнит открытое состояние и пытается её размотать ещё больше. Может и ничего страшного, конечно. Но точно потребует ручной настройки, чтобы пришло в норму.

Думаю, вариант, как сейчас, всё-таки оптимальный. Но опцию сохранения положения запишу в to do, постараюсь сделать, для тех, кому оно нужно.

andrew-moiseyev, 2022-02-02:
Собрали NodeMCU + драйвер + мотор, без концевика. Начали крутить - тесты крутят в обе стороны, вниз - крутит вверх. Напоминания не читали, разумеется. Может, в сетапе ставить флаг "wasMoved=false" и пока ни разу не крутили - показывать предупреждение _над_ кнопками красным/заметным цветом? С чекбоксом "да понял я, не показывайте больше".

andrew-moiseyev, 2022-02-02:
И на сайт бы ссылку на гитхаб.

ACE1046, 2022-02-02:
Принято, продумаю этот момент. Этот Issue пусть повисит открытым, чтобы не забыть.

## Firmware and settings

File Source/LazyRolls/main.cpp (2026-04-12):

/*
LazyRolls
(C) 2019-2022 ACE, a_c_e@mail.ru
http://imlazy.ru/rolls/

21.12.2018 v0.04 beta
21.02.2019 v0.05 beta
16.03.2019 v0.06
10.04.2019 v0.07
02.06.2020 v0.08
29.01.2021 v0.09
30.03.2021 v0.10
05.08.2021 v0.11
27.01.2022 v0.12
09.12.2022 v0.13
20.04.2023 v0.14
16.01.2024 v0.15

*/
#ifdef ESP8266
	#include <ESP8266WiFi.h>
	#include <ESP8266WebServer.h>
	#include <ESP8266HTTPUpdateServer.h>
	#include <ESP8266HTTPClient.h>
	#include <ping.h>
	#include <FS.h>
#else
	#include <WiFi.h>
	#include <WebServer.h>
	#include <HTTPUpdateServer.h>
	#include <HTTPClient.h>
	#include "ping32.h"
	#include "FS.h"
	#include <LittleFS.h>
//	#include <rom/rtc.h> // for reset reason
	#if CONFIG_IDF_TARGET_ESP32C3
	#include "esp32c3/rom/spi_flash.h"
	#endif
	//#include "driver/gpio.h"
	//gpio_get_level(gpio_num_t gpio_num);
	#include "hal/gpio_hal.h"
	#include "driver/temperature_sensor.h"
	#define SPIFFS LittleFS
	#define GPOS GPIO.out_w1ts.val
	#define GPOC GPIO.out_w1tc.val
	#define GPI GPIO.in.val
	#include <esp_task_wdt.h>
	#define ESP32_WDT_TIMEOUT 10000  // WDT timeout
#endif
#include <WiFiUdp.h>
#include <DNSServer.h>
#include <time.h>
#include "settings.h"
extern "C" {
#include "lwip/etharp.h" // gratuitous arp
#include "lwip/tcpip.h" // gratuitous arp
}

#define VERSION "0.15.6"
#define MQTT 1 // MQTT & HA functionality
#define ARDUINO_OTA 1 // Firmware update from Arduino IDE
#define MDNSC 1 // mDNS responder. Required for ArduinoIDE web port discovery
#define DAYLIGHT 1 // Sunrise functions
#define RF 1 // RF receiver support
#define SPIFFS_AUTO_INIT
#define SWAP_AB_CD 0

#if FLASH_MAP_SUPPORT
#define AUTOMEMSIZE
#include <flash_hal.h>
// Custom memory map, 128K SPIFFS for 1MB modules, 1M for 4MB
#define FLASH_MAP_LAZYROLL \
	{ \
		{ .eeprom_start = 0x402fb000, .fs_start = 0x402db000, .fs_end = 0x402fb000, .fs_block_size = 0x1000, .fs_page_size = 0x100, .flash_size_kb = 1024 }, \
		{ .eeprom_start = 0x403fb000, .fs_start = 0x403c0000, .fs_end = 0x403fb000, .fs_block_size = 0x1000, .fs_page_size = 0x100, .flash_size_kb = 2048 }, \
		{ .eeprom_start = 0x405fb000, .fs_start = 0x40500000, .fs_end = 0x405fa000, .fs_block_size = 0x2000, .fs_page_size = 0x100, .flash_size_kb = 4096 }, \
		{ .eeprom_start = 0x409fb000, .fs_start = 0x40400000, .fs_end = 0x409fa000, .fs_block_size = 0x2000, .fs_page_size = 0x100, .flash_size_kb = 8192 }, \
		{ .eeprom_start = 0x411fb000, .fs_start = 0x40400000, .fs_end = 0x411fa000, .fs_block_size = 0x2000, .fs_page_size = 0x100, .flash_size_kb = 16384 }, \
		{ .eeprom_start = 0x4027b000, .fs_start = 0x40273000, .fs_end = 0x4027b000, .fs_block_size = 0x1000, .fs_page_size = 0x100, .flash_size_kb = 512 }, \
	}
  FLASH_MAP_SETUP_CONFIG(FLASH_MAP_LAZYROLL);
#endif

#include "spiff_files.h"

#if MDNSC
	#ifdef ESP8266
		#include <ESP8266mDNS.h>
	#else
		#include <ESPmDNS.h>
	#endif
#endif

#if MQTT
	// For MQTT support: Sketch - Include Library - Manage Libraries - PubSubClient - Install
	#include <PubSubClient.h>
#endif

#if ARDUINO_OTA
	#include <ArduinoOTA.h>
#endif

#if RF
	// For RF support: Sketch - Include Library - Manage Libraries - rc-switch by Suat Ozgur - Install
	#include "RCSwitch.h"
	RCSwitch mySwitch = RCSwitch();
#endif

#if DAYLIGHT
	#include "daylight.h"
#endif

// copy "wifi_settings.example.h" to "wifi_settings.h" and modify it, if you wish
// Or comment next string and change defaults in this file
//#include "wifi_settings.h"

#ifndef SSID_AND_PASS
// if "wifi_settings.h" not included
const char def_ssid[] PROGMEM = ""; // Empty ssid to create SoftAP at start
const char def_password[] PROGMEM = "";
const char def_ntpserver[] PROGMEM = "ru.pool.ntp.org";
const char def_hostname[] PROGMEM = "lazyroll-%06X";
const char def_mqtt_server[] PROGMEM = "mqtt.lan";
const char def_mqtt_login[] PROGMEM = "";
const char def_mqtt_password[] PROGMEM = "";
const uint16_t def_mqtt_port=1883;
const char def_mqtt_topic_state[] PROGMEM = "lazyroll/%HOSTNAME%/state";
const char def_mqtt_topic_command[] PROGMEM = "lazyroll/%HOSTNAME%/command";
const char def_mqtt_topic_alive[] PROGMEM = "lazyroll/%HOSTNAME%/alive";
const char def_mqtt_topic_aux[] PROGMEM = "lazyroll/%HOSTNAME%/aux";
const char def_mqtt_topic_info[] PROGMEM = "lazyroll/%HOSTNAME%/info";
#endif

//char *temp_host;
const char* update_path = "/update2";
const char* update_username = "admin";
const char* update_password = "admin";
uint16_t def_step_delay_mks = 1500;
#define FAV_FILE "/favicon.ico"
#define CLASS_FILE "/styles.css"
#define JS_FILE "/scripts.js"
#define INI_FILE "/settings.ini"
#define POS_FILE "/position.dat"
#ifdef ESP8266
#define PIN_SWITCH 14
#if SWAP_AB_CD
#define PIN_A 13
#define PIN_B 12
#define PIN_C 5
#define PIN_D 4
#else
#define PIN_A 5
#define PIN_B 4
#define PIN_C 13
#define PIN_D 12
#endif
#define PIN_EN 4
#define PIN_ST 13
#define PIN_DR 12
#define PIN_LED 2
uint8_t PIN_PWM = 15;
#else
#define PIN_SWITCH 7
#define PIN_A 4
#define PIN_B 3
#define PIN_C 6
#define PIN_D 5
#define PIN_EN 3
#define PIN_ST 6
#define PIN_DR 5
#define PIN_LED 8
//#define PIN_PWM 4 // ?
uint8_t PIN_PWM = 4;
#define PIN_ADC 0 // voltage
#endif
#define PIN_ENC_A PIN_C
#define PIN_ENC_B PIN_D
#define DIR_UP (-1)
#define DIR_DN (1)
#define MAX_PINOUT 8 // Motor types. 3xStepper + 1 step/dir + 4 DC/PWM/Enc
#define DEFAULT_UP_SAFE_LIMIT 300 // make extra rotations up if not hit switch
#define DEFAULT_SWITCH_IGNORE_STEPS 100 // ignore endstop for first step on moving down
#define MIN_STEP_DELAY 50 // minimal motor step time in mks
#define UART_PING_INTERVAL_MS (30*1000) // Master ping slaves every 30 seconds
#define SLAVE_MAX_NO_PING_MS (70*1000) // Enable WiFi in slave mode if no ping from master
#define SLAVE_SLEEP_TIMEOUT_MS (180*1000) // Disable WiFi in slave mode after network idle
#define PINGER_WARN 4 // Log sfter N ping fails
#define PINGER_ACTION 7 // Action (log/reconnect/reboot) after N ping fails
#define PINGER_INTERVAL_S 60 // Ping interval, seconds
#define PINGER_REPEAT_INTERVAL_S 10 // Ping interval after ping fail, seconds
#define ALARMS 10
#define DAY (24*60*60) // day length in seconds
#define STRINGIFY(x) #x
#define TOSTRING(x) STRINGIFY(x)
#define ARRAYSIZE(arr) (sizeof(arr) / sizeof(arr[0]))
#define MASTER (ini.slave == 255)
#define SLAVE (ini.slave != 255 && ini.slave != 0)
#define ADDR_MASTER 0
#define ADDR_SELF_ONLY 0
#define ADDR_ALL 255
#define ADDR_DEFAULT 254
#define MQTT_INFO_SECONDS 1*60 // Send mqtt info (rssi, uptime, etc) every N seconds
#define MOTOR_OFF_DELAY 10000 // Delay before powering off stepper motor (around 1 sec)
#define STEPS_BREAKING 25 // Decrease speed on last steps

const int Languages = 2;
const char ru_ru[] PROGMEM = "Русский";
const char en_en[] PROGMEM = "English";
const __FlashStringHelper *Language[Languages]={ (__FlashStringHelper*)en_en, (__FlashStringHelper*)ru_ru };
const PROGMEM char *onoff[][Languages]={{"off", "on"}, {"выкл", "вкл"}};

const uint8_t steps[3][4]={
	{PIN_A, PIN_C, PIN_B, PIN_D},
	{PIN_A, PIN_B, PIN_D, PIN_C},
	{PIN_A, PIN_B, PIN_C, PIN_D}
};

const uint8_t hardware_pins[] = { 0, 0, 2, 3, 15 }; // available GPIOs, must correspond to next line
#define PIN_LIST F("0,\"---\",1,\"GPIO0 (D3/DTR) - Gnd\",2,\"GPIO2 (D4) - Gnd\",3,\"GPIO3 (RX) - Gnd\",4,\"GPIO15 (D8) - 3.3V\"")

volatile int position; // current motor steps position. 0 - at main endstop
volatile int roll_to; // position to go to
uint16_t step_c[8], step_s[8]; // bitmasks for every step
volatile uint8_t endstop_hit = 0; // endstop hit flag. Set at ISR, reset at user level
volatile int endstop_hit_pos = 0; // position of endstop hit
volatile bool TestMode = 0; // Ignoring endstop in test mode
bool voltage_available = 0;
uint32_t last_network_time = 0; // last network activity time
bool WiFi_active = false;
bool WiFi_connected = false;
bool WiFi_AP_disabled = false; // AP mode disabled after successfull connection to home network or after first ping msg from master
int WiFi_attempts = 0;
unsigned long last_reconnect = 0;
uint32_t uart_crc_errors = 0;
#define MAX_RECONNECT_ATTEMPS 2 // reconnect attemps before creating Access Point
bool rf_page_open = 0; // true while RF settings open
bool mem_problem = 0; // memory error flag, incorrect compile settings
volatile uint8_t pwm_LED = 0; // software LED PWM. 0 - disabled
uint16_t pwm_phase_low_ticks, pwm_phase_high_ticks;
volatile bool virtual_endstop_hit = 0;
uint16_t ticks_per_step = 4; // timer ticks per motor step, used for soft start
uint8_t Master_IP = 0; // Master's IP, last byte. Slaves report to it after wakeup
uint8_t Slaves_IP[6]; // IPs of slaves after they woke up

#ifdef ESP8266
	ESP8266WebServer httpServer(80);
	ESP8266HTTPUpdateServer httpUpdater;
#else
	WebServer httpServer(80);
	HTTPUpdateServer httpUpdater;
	temperature_sensor_handle_t temp_handle = NULL;
#endif	
WiFiClient espClient;

typedef struct {
	uint16_t time;
	uint16_t tmin; // minimal time to sun option
	uint8_t percent_open; // 0 - open, 100 - close, 101-105 - presets
	uint8_t day_of_week; // LSB - monday
	uint8_t flags;
	uint8_t m_s; // master / slaves bitmask
	uint32_t reserved;
} alarm_type;
#define ALARM_FLAG_ENABLED 0x01
#define ALARM_FLAG_SUNRISE 0x02
#define ALARM_FLAG_SUNSET  0x04
#define ALARM_FLAG_SLOW    0x08

typedef struct {
	uint32_t code;
	uint8_t action;
	uint8_t flags; // reserved
	uint16_t reserved;
} rf_cmd_type;
#define RF_FLAG_STOP2ND 0x01

typedef struct {
	uint8_t num; // slave group number
	uint8_t ip4; // ip address last byte, 0 = empty
	uint16_t reserved;
} ip_slave_type;

typedef struct {
	int pos;
	uint32_t flash_writes;
} flash_pos_type;
#define UNKNOWN_POS (INT_MIN)

#define MAX_SLAVE 5
#define MAX_IP_SLAVE 10
#define MAX_PRESETS 5
#define MAX_RF_CMDS 10
struct {
	char hostname[16+1];
	char ssid[32+1];
	char password[32+1];
	char ntpserver[32+1];
	int32_t lang;
	uint8_t pinout; // index in "steps" array, according to motor wiring
	bool reversed; // up-down reverse
	uint16_t step_delay_mks; // delay (mks) for each step of motor
	int32_t timezone; // timezone in minutes relative to UTC
	int32_t full_length; // steps from open to close
	uint32_t spiffs_time; // time of files in spiffs for version checking
	alarm_type alarms[ALARMS];
	uint8_t switch_reversed; // reverse switch logic. 0 - NC, 1 - NO
	bool mqtt_enabled;
	char mqtt_server[64+1]; // MQTT server, ip or hostname
	uint32_t mqtt_port;
	char mqtt_login[64+1]; // MQTT server login
	char mqtt_password[64+1]; // MQTT server password
	uint16_t mqtt_ping_interval; // I'm alive ping interval, seconds
	char mqtt_topic_state[127+1]; // publish current state topic
	char mqtt_topic_command[127+1]; // subscribe to commands topic
	uint8_t mqtt_state_type; // percents, ON/OFF, etc
	uint16_t switch_ignore_steps; // ignore endstop for first step on moving down
	uint8_t led_mode; // Default blue LED mode
	uint8_t led_level; // Default blue LED brightness
	uint16_t preset[MAX_PRESETS]; // Position (steps) for preset 1-5
	bool mqtt_discovery; // Home Assistant MQTT Discovery enabled
	uint8_t sw_at_bottom; // 0 - switch at opened position, 1 - switch at closed position
	uint8_t mqtt_invert; // mqtt percents inverted, 0% = closed
	char mqtt_topic_alive[127+1]; // publish availability topic (Birth & LWT)
	int32_t up_safe_limit; // make extra rotations up if not hit switch
	uint8_t btn1_pin; // hardware button pin selection
	uint8_t btn_mode; // auto/mqtt report (reserved)
	uint8_t slave; // master/slave mode
	uint8_t aux_pin; // auxiliary pin selection
	char mqtt_topic_aux[127+1]; // auxiliary input topic
	char mqtt_topic_info[127+1]; // information topic (IP, RSSI, etc)
	char name[64+1]; // Name
	ip4_addr ip, mask, gw, dns; // Network config
	rf_cmd_type rf_cmd[MAX_RF_CMDS]; // RF433 commands
	uint8_t rf_pin; // RF remote input pin
	int32_t lat; // latitude
	int32_t lng; // longitude
	uint8_t btn2_pin; // hardware button pin selection
	uint8_t btn1_click, btn2_click; // Action on button click
	uint8_t btn1_long, btn2_long; // Action on button long click
	uint8_t btn1_c_addr, btn2_c_addr; // Button click, master and slaves selection, bitmask
	uint8_t btn1_l_addr, btn2_l_addr; // Long click, master and slaves selection, bitmask
	char ap_pswd[16+1]; // Access Point password
	uint8_t end2_pin; // second endstop pin selection
	uint8_t switch2_reversed; // reverse second switch logic. 0 - NC, 1 - NO
	uint16_t step_delay_mks2; // delay (mks) for each step of motor, 2nd speed
	uint8_t ping_enabled; // pinger watchdog enabled
	uint8_t ping_act; // action on no ping response
	ip4_addr ping_ip; // ip address for pinger
	ip_slave_type ip_slaves[MAX_IP_SLAVE]; // ip slaves list
	uint8_t save_pos_to_flash; // save current position
	uint16_t city; // selected city
	char posix_tz[45]; // POSIX format timezone
	uint8_t off_delay; // 5 sec stepper motor off delay
} ini;

// language functions
const char * L(const char *s1, const char *s2)
{
	return (ini.lang == 0) ? s1 : s2;
}
const __FlashStringHelper *FL(const __FlashStringHelper *s1, const __FlashStringHelper *s2)
{
	return (ini.lang == 0) ? s1 : s2;
}
#define FLF(a, b) FL(F(a), F(b))
String SL(const char *s1, const char *s2)
{
	return (ini.lang == 0) ? String(s1) : String(s2);
}
String SL(String s1, String s2)
{
	return (ini.lang == 0) ? s1 : s2;
}

uint32_t ESP_getChipId()
{
	uint32_t id;
#ifdef ESP8266	
	id = ESP.getChipId();
#else
	id = ESP.getEfuseMac() >> 24; // Get MAC (in reversed format), cut last 3 bytes
	id = (id >> 16) | (id & 0xFF00) | ((id & 0xFF) << 16); // reverse it
#endif
	return id;
}

void ESP_setSleepMode(bool enable)
{
#ifdef ESP8266
	WiFi.setSleepMode(enable ? WIFI_MODEM_SLEEP : WIFI_NONE_SLEEP);
#else
	WiFi.setSleep(enable);
#endif
}

static uint32_t ESP_getFlashChipId()
{
#ifdef ESP8266
	return ESP.getFlashChipId();
#else
	uint32_t id = 0;
#if CONFIG_IDF_TARGET_ESP32C3
	id = g_rom_flashchip.device_id;
#endif
	id = ((id & 0xff) << 16) | ((id >> 16) & 0xff) | (id & 0xff00);
	return id;
#endif
}

void NetworkActivity(void)
{
	ESP_setSleepMode(false);
	last_network_time = millis();
}

#define SPEED2 (-1)
void ToPercent(uint8_t pos, uint8_t address = ADDR_ALL, int step_delay = 0);
void ToPosition(int pos, uint8_t address = ADDR_ALL, int step_delay = 0);
void ToPreset(uint8_t preset, uint8_t address = ADDR_ALL, int step_delay = 0);
void Open(uint8_t address = ADDR_ALL, int step_delay = 0);
void Close(uint8_t address = ADDR_ALL, int step_delay = 0);
void Stop(uint8_t address);
void ButtonClick(uint8_t btnnumber, uint8_t address);
void ButtonLongClick(uint8_t btnnumber, uint8_t address);
void WiFi_On();
void WiFi_Off();
uint32_t getTimeUTC();
String MakeNode(const __FlashStringHelper *name, String val);
void CalcAlarmTimes();
void AdjustTimerInterval(int step_delay_mks = 0); // 0 - default, -1 - 2nd speed
void WritePosition(int pos);
void SaveCurrentPosition();

//===================== Event Logger ===================================

#define MAX_LOG_ENTRIES 32

const char ET_Err1[] PROGMEM = "Error 01";
const char ET_NTP_Sync[] PROGMEM = "NTP time syncronized";
const char ET_Settings_Loaded[] PROGMEM = "Settings loaded";
const char ET_Settings_Saved[] PROGMEM = "Settings saved";
const char ET_Settings_Not_Loaded[] PROGMEM = "Settings set to default";
const char ET_Cmd_Stop[] PROGMEM = "Stop";
const char ET_Cmd_Open[] PROGMEM = "Open";
const char ET_Cmd_Close[] PROGMEM = "Close";
const char ET_Cmd_Percent[] PROGMEM = "Go to percent";
const char ET_Cmd_Steps[] PROGMEM = "Go to steps";
const char ET_Cmd_Preset[] PROGMEM = "Go to preset";
const char ET_Cmd_Click[] PROGMEM = "Click btn 1";
const char ET_Cmd_LClick[] PROGMEM = "Long click btn 1";
const char ET_Cmd_Click2[] PROGMEM = "Click btn 2";
const char ET_Cmd_LClick2[] PROGMEM = "Long click btn 2";
const char ET_Slave_No_Ping[] PROGMEM = "No ping from master, enabling WiFi";
const char ET_Wifi_Close_AP[] PROGMEM = "Reconnected to network in STA mode. Closing AP";
const char ET_Wifi_Reconnect[] PROGMEM = "Trying to reconnect";
const char ET_Wifi_Got_IP[] PROGMEM = "IP address";
const char ET_Wifi_Start_AP[] PROGMEM = "Starting soft AP";
const char ET_Wifi_Disconnect[] PROGMEM = "WiFi disconnected";
const char ET_Endstop_Hit[] PROGMEM = "Stopped at endstop";
const char ET_Endstop_Hit_Error[] PROGMEM = "Stopped at endstop on going down";
const char ET_MQTT_Connect[] PROGMEM = "MQTT connected";
const char ET_MQTT_Connecting[] PROGMEM = "Connecting to MQTT... ";
const char ET_Started[] PROGMEM = "Started";
const char ET_Stall[] PROGMEM = "Motor stalled";
const char ET_Auto[] PROGMEM = "Open/Close";
const char ET_Cmd_Zero[] PROGMEM = "Zero reset";
const char ET_Pingfail[] PROGMEM = "Ping failed ";
const char ET_Cmd_Wakeup[] PROGMEM = "Wake up";
const char ET_IP_Slave_Err[] PROGMEM = "WiFi slave error";

const char EQ_HTTP[] PROGMEM = "Src: HTTP";
const char EQ_MQTT[] PROGMEM = "Src: MQTT";
const char EQ_UART_MASTER[] PROGMEM = "Src: TX/RX master";
const char EQ_HTTP_MASTER[] PROGMEM = "Src: WIFI master";
const char EQ_SCHEDULE[] PROGMEM = "Src: Scheduler";
const char EQ_BUTTON[] PROGMEM = "Src: Button";
const char EQ_RF[] PROGMEM = "Src: RF";

enum EVENT_LEVEL { EL_NONE = 0, EL_DEBUG, EL_INFO, EL_WARN, EL_ERROR };
enum EVENT_ID                           { EI_Err1, EI_NTP_Sync, EI_Settings_Loaded, EI_Settings_Saved, EI_Settings_Not_Loaded, EI_Cmd_Stop, EI_Cmd_Open, EI_Cmd_Close,
	EI_Cmd_Percent, EI_Cmd_Steps, EI_Cmd_Preset, EI_Cmd_Click, EI_Cmd_LClick, EI_Cmd_Click2, EI_Cmd_LClick2, EI_Slave_No_Ping, EI_Wifi_Close_AP, EI_Wifi_Reconnect,
	EI_Wifi_Got_IP, EI_Wifi_Start_AP, EI_Endstop_Hit, EI_Endstop_Hit_Error, EI_MQTT_Connect, EI_MQTT_Connecting, EI_Started, EI_Wifi_Disconnect, EI_Stall, EI_Auto,
	EI_Cmd_Zero, EI_Pingfail, EI_Cmd_Wakeup, EI_IP_Slave_Err };
const char* const event_txt[] PROGMEM = { ET_Err1, ET_NTP_Sync, ET_Settings_Loaded, ET_Settings_Saved, ET_Settings_Not_Loaded, ET_Cmd_Stop, ET_Cmd_Open, ET_Cmd_Close,
	ET_Cmd_Percent, ET_Cmd_Steps, ET_Cmd_Preset, ET_Cmd_Click, ET_Cmd_LClick, ET_Cmd_Click2, ET_Cmd_LClick2, ET_Slave_No_Ping, ET_Wifi_Close_AP, ET_Wifi_Reconnect,
	ET_Wifi_Got_IP, ET_Wifi_Start_AP, ET_Endstop_Hit, ET_Endstop_Hit_Error, ET_MQTT_Connect, ET_MQTT_Connecting, ET_Started, ET_Wifi_Disconnect, ET_Stall, ET_Auto,
	ET_Cmd_Zero, ET_Pingfail, ET_Cmd_Wakeup, ET_IP_Slave_Err };

enum EVENT_SRC                              { ES_HTTP, ES_MQTT, ES_UART_MASTER, ES_HTTP_MASTER, ES_SCHEDULE, ES_BUTTON, ES_RF };
const char* const event_src_txt[] PROGMEM = { EQ_HTTP, EQ_MQTT, EQ_UART_MASTER, EQ_HTTP_MASTER, EQ_SCHEDULE, EQ_BUTTON, EQ_RF };

typedef struct {
	uint32_t time; // timecode
	uint32_t val; // value
	uint8_t event; // event code
	uint8_t level; // severity level
	uint16_t flags; // reserved
} LogEntry;

#if MAX_LOG_ENTRIES < 255
	typedef uint8_t idx;
#else
	typedef uint16_t idx;
#endif

class Log
{
private:
	idx head, count;
	LogEntry log[MAX_LOG_ENTRIES]; // 12*32 = 384 bytes of RAM
public:
	Log();
	~Log();
	void Add(uint8_t event, uint8_t level, uint32_t val);
	const LogEntry* Get(idx offset);
	idx Count();
};

Log::Log()
{
	head = count = 0;
}

Log::~Log()
{
}

void Log::Add(uint8_t event, uint8_t level, uint32_t val)
{
	uint32_t time;
	time = getTimeUTC();
	if (!time) time = millis() / 1000;
	log[head].event = event;
	log[head].level = level;
	log[head].time = time;
	log[head].val = val;
	head++;
	if (head >= MAX_LOG_ENTRIES) head = 0;
	if (count < MAX_LOG_ENTRIES) count++;
}

const LogEntry* Log::Get(idx offset)
{ // offset from head, 0 - last entry
	idx i;
	if (offset >= count) return 0;
	if (head > offset)
		i = head - offset - 1;
	else
		i = MAX_LOG_ENTRIES - offset + head - 1;
	return &log[i];
}

idx Log::Count()
{
	return count;
}

Log elog;

//===================== LED ============================================

typedef enum { LED_OFF = 0, LED_ON, LED_MQTT, LED_HTTP, LED_MQTT_HTTP, LED_ALIVE, LED_BUTTON, LED_MODE_MAX } led_modes;
typedef enum { LED_LOW = 0, LED_MED, LED_HIGH, LED_LEVEL_MAX } led_levels;
uint8_t led_mode;
uint8_t led_level;

const __FlashStringHelper* LEDModeString(uint8_t mode = 0xFF)
{
	if (mode == 0xFF) mode = led_mode;
	if (mode == LED_OFF) return FLF("Off", "Выключен");
	if (mode == LED_ON) return FLF("On", "Включен");
	if (mode == LED_MQTT) return FLF("On MQTT commands", "При MQTT командах");
	if (mode == LED_HTTP) return FLF("On HTTP requests", "При HTTP запросах");
	if (mode == LED_MQTT_HTTP) return FLF("On MQTT and HTTP", "При MQTT и HTTP");
	if (mode == LED_ALIVE) return FLF("Blink alive", "Мигать периодически");
	if (mode == LED_BUTTON) return FLF("On button press", "По нажатию кнопки");
	return F("");
}
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
void loop(void)
{
	ProcessWiFi();
	if (!ini.mqtt_enabled) GratuitousARP();
	ProcessLED();
	ProcessRF();

	httpServer.handleClient();
	Process_OTA();
	SyncNTPTime();
	Scheduler();
	if (!SLAVE) ProcessMQTT();
	CP_process();
	process_Button();
	process_Aux();
	if (MASTER) SendUARTPing();
	if (SLAVE) ProcessUART();
	MotorFailsafe();
	ProcessPing();
	SaveCurrentPosition();
	ProcessMDNS();

	if (millis() - last_network_time > 10000)
		ESP_setSleepMode(true);
	if (SLAVE && WiFi_active &&
		(millis() - last_network_time > SLAVE_SLEEP_TIMEOUT_MS) &&
		(millis() - lastUARTping < SLAVE_MAX_NO_PING_MS))
	{
		Serial.println(F("Network idle. WiFi shutdown"));
		WiFi_Off();
	}
	if (endstop_hit != EL_NONE)
	{
		if (endstop_hit == EL_ERROR)
			elog.Add(EI_Endstop_Hit_Error, EL_ERROR, endstop_hit_pos);
		else
			elog.Add(EI_Endstop_Hit, EL_INFO, endstop_hit_pos);
		endstop_hit = EL_NONE;
	}

#ifdef ESP32
	esp_task_wdt_reset();
#endif
	delay(10); // this delay enables light sleep mode
	// static int heap = 65536;
	// int h;
	// h = ESP.getFreeHeap();
	// if (h < heap)
	// {
	// 	heap = h;
	// 	Serial.println(heap);
	// }

/* 	// cpu load test
	static uint32_t ms;
	if (millis() - ms > 10000)
	{
		ms = millis();
		Serial.println(ESP.getCpuFreqMHz());

		uint32_t t1=millis();
		for (i=0; i<1000000; i++) ;
		Serial.println(millis()-t1);
	}
*/
}

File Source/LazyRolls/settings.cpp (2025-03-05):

// settings module for esp8266 projects
// stores config in SPIFFS
// (C) 2018 ACE

#include <string.h>
#if defined(ESP8266)
  #include <FS.h>
#else
  #include <LittleFS.h>
  #define FORMAT_LITTLEFS_IF_FAILED true
  #define SPIFFS LittleFS
#endif

#define INIFILE "/settings.ini"
#define ZEROCRC 0xAC

bool spiffsActive = false;

bool Init()
{
  if (spiffsActive) return true;
  if (SPIFFS.begin()) 
    spiffsActive = true;
  else
    Serial.println("Unable to activate SPIFFS");
  return spiffsActive;
}

bool LoadSettings(void *ini, int len)
{
  int r, i;
  uint8_t crc;
  if (!Init()) return false;
  
  if (!SPIFFS.exists(INIFILE)) 
  {
    Serial.println("No settings file");
    return false;
  }

  File f = SPIFFS.open(INIFILE, "r");
  if (!f)
  {
    Serial.println("Unable to read settings");
    return false;
  } 

  f.read(&crc, sizeof(crc));
  r=f.read((uint8_t*)ini, len);

  for (i=0; i<r; i++) crc ^= ((uint8_t*)ini)[i];
  
  f.close();

  if (crc!=ZEROCRC) Serial.println("Settings CRC error");

  return (crc==ZEROCRC);
}

bool SaveSettings(void *ini, int len)
{
  int i;
  uint8_t crc;
  if (!Init()) return false;
  
  File f = SPIFFS.open(INIFILE, "w");
  if (!f)
  {
    Serial.println("Unable to write settings");
    return false;
  } 

  crc=ZEROCRC;
  for (i=0; i<len; i++) crc ^= ((uint8_t*)ini)[i];

  f.write(&crc, sizeof(crc));
  f.write((uint8_t*)ini, len);

  f.close();
  return true;
}

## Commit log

2018-04-04 V0.01 beta
    [Motor_bracket.scad, Motor_bracket.stl, Shaft.scad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]
2018-04-16 Modified for PCB ordering. Added Gerber.
2018-04-18 Fix: close after reboot
    [Curtains.ino]
2018-04-25 Small update, shaft end made conical
    [Motor_bracket.scad, Motor_bracket.stl, Shaft.scad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]
2018-05-24 Fixed bug with packet loss in AP mode
    [Curtains.ino]
2018-05-29 Create BoM.txt
    Bill of Material. Чтобы не искать.
2019-04-10 v0.07 Switch ignore zone adjustable, software pull-up
2020-01-28 Test firmware. Update to 2.6.3. Blinks blue LED every 10 seconds.
2020-06-28 Screw mount
    [mount_screw.scad, mount_screw.stl]
2021-01-28 Endstop at bottom
2021-01-29 MQTT discovery fix, invert percent
    [Curtains.ino]
2021-02-11 Board for Nema17 stepper drivers
2021-02-24 Switch ignore reset on open
    [Curtains.ino]
2021-02-24 Switch ignore /8 bug fixed
    [Curtains.ino]
2021-03-22 Voltage accuracy increased
2021-03-23 Up safe limit moved to settings. Hardware button.
2021-03-30 Nema17 board
2021-04-23 Board update
2021-04-24 Board optimizations
2021-08-05 mqtt info, new HA sensors
2021-11-13 Добавлены команды click, longclick
2021-11-14 название шторы
2021-11-23 Log count in XML and http, endstop on closing
2021-11-24 Log auto update, reboot reason
    [main.cpp, scripts.js]
2022-02-03 Bugfix: negative positions in log file
    [main.cpp]
2022-02-22 En/step/dir pin mode initialization (in case if different from A/B/C/D pins)
2022-03-23 small fix, ini.full_length max at 999999
    [main.cpp]
2022-11-30 Suntime update, memory warning, button double click fix
    [main.cpp]
2022-12-05 Button addresses save&load, auto headers generation at build
2022-12-05 Test mode ignores endstop
2022-12-07 Support of 2 buttons with actions/slaves selection
2022-12-08 Кнопки пресетов и ведомых на главной
2023-01-26 v0.13.1 HA voltage unit of measurement added
2023-01-29 DC motor support
2023-01-29 DC motor function preview
2023-03-16 DC motor
2023-03-16 DC motor interrupts
2023-03-17 Encoder fail safe
2023-03-17 MQTT report, endstop, status:opening
2023-03-17 Motor settings interface
2023-03-18 Nema17 schematics & gerbers bugfix
2023-03-21 Motor enc update, RF commands button
2023-03-23 Second endstop
2023-03-23 PWM fix
2023-04-19 HA sensor uptime changed to last restart time
2023-11-09 Fix: incorrect work of button with switch at bottom
    [main.cpp]
2023-11-18 Вторая скорость с кнопок
2023-12-27 Slave wake up buttons
2025-03-05 ESP32(C3) support
2025-03-06 v0.15.4 ESP32C3 support (betatest)
2025-03-07 Arduino core version on information page
2026-04-07 * Для шаговых двигателей добавлена плавная остановка при движении вниз и удержание в течение ~1 сек после остановки, для предотвращения разматывания шторы по инерции. * Для DC моторов можно регулиров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
2026-04-10 Uptime overflow at 49 days fixed
    [main.cpp]
2026-04-12 motor off-delay setting, bugfix
    [main.cpp]
